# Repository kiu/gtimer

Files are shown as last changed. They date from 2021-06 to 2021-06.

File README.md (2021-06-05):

# gtimer
gtimer is a programmable controller for the GARDENA [Fully Automatic Flower Box Watering](https://www.gardena.com/int/products/watering/holiday-watering/fully-automatic-flower-box-watering/900916701/) drip system.
Thanks to an ATMEGA microcontroller and a RTC module very flexible watering plans can be achieved. In addition a temperature module influences the timings based on ambient temperature during the course of the day.

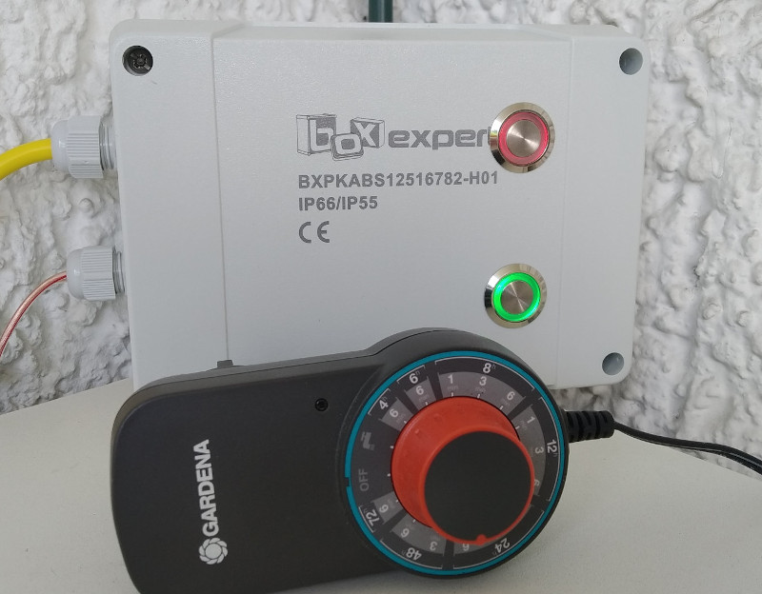
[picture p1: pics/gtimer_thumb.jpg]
gtimer


gtimer is a drop-in replacement for the GARDENA timer connecting to the original pump of the system.

# Warning
Be aware of what you are doing. You are playing with water and mains voltage in an outdoor environment.
Not only might this kill you, it will hurt the whole time you're dying.

# Nitty-Gritty Details
Checkout the [pics](https://github.com/kiu/gtimer/tree/master/pics) and [hardware](https://github.com/kiu/gtimer/tree/master/hardware) section including BOM, Schematic, PCB layout, firmware, etc.

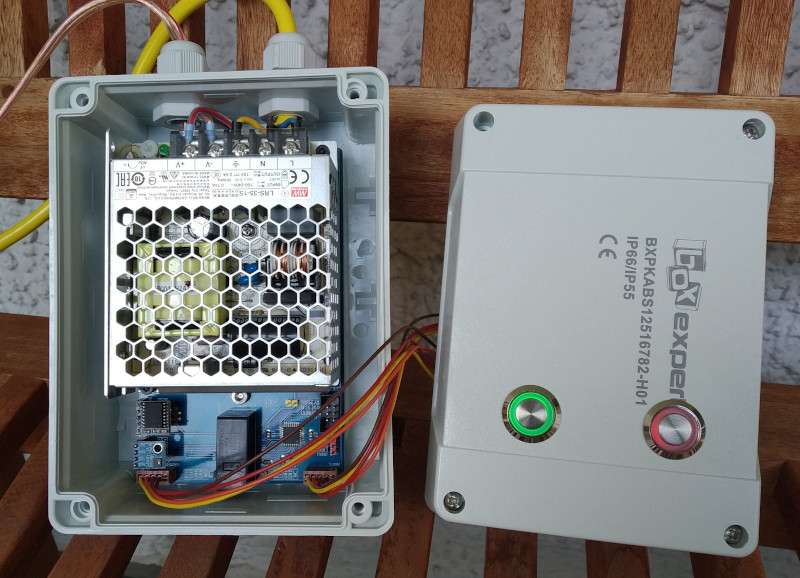
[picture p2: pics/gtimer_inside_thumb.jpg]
gtimer


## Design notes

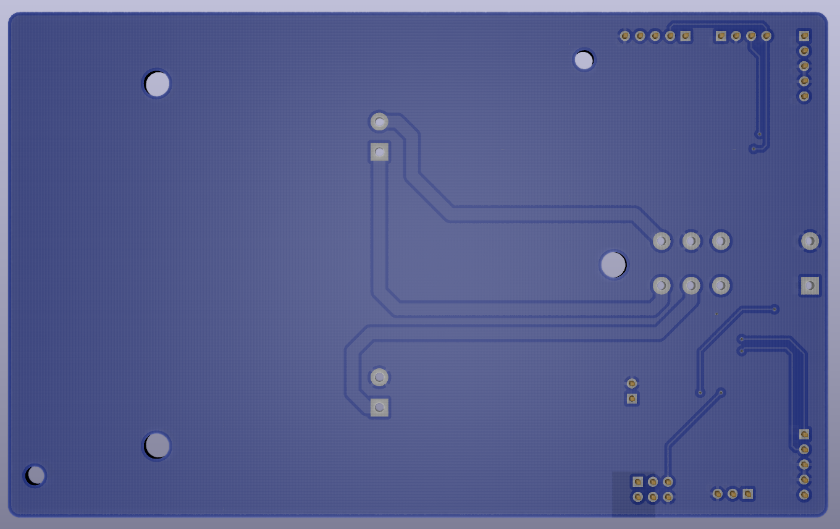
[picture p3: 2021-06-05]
hardware/kicad_gtimer_render_bottom.png

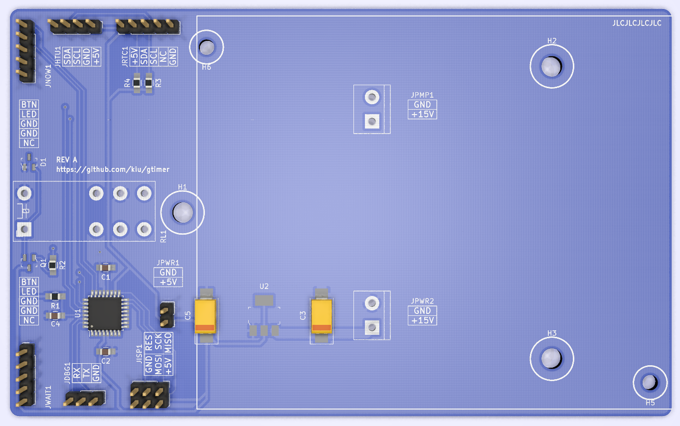
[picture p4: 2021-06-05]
hardware/kicad_gtimer_render_front.png

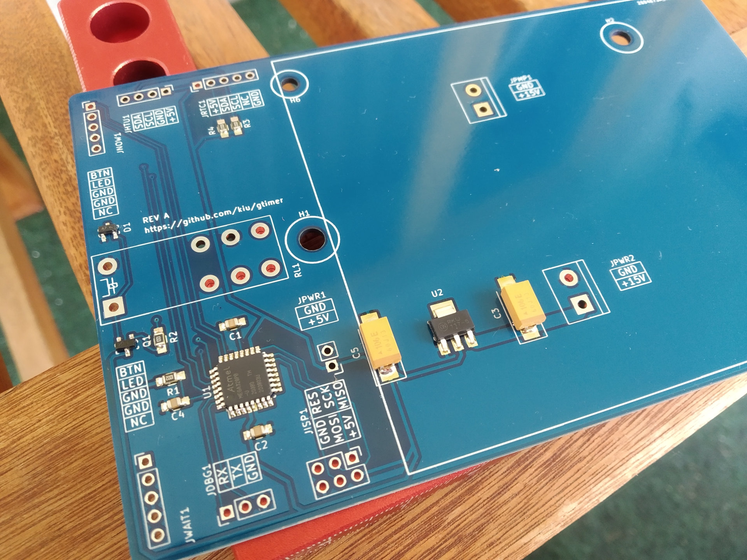
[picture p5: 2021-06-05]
pics/gtimer_reflow.jpg

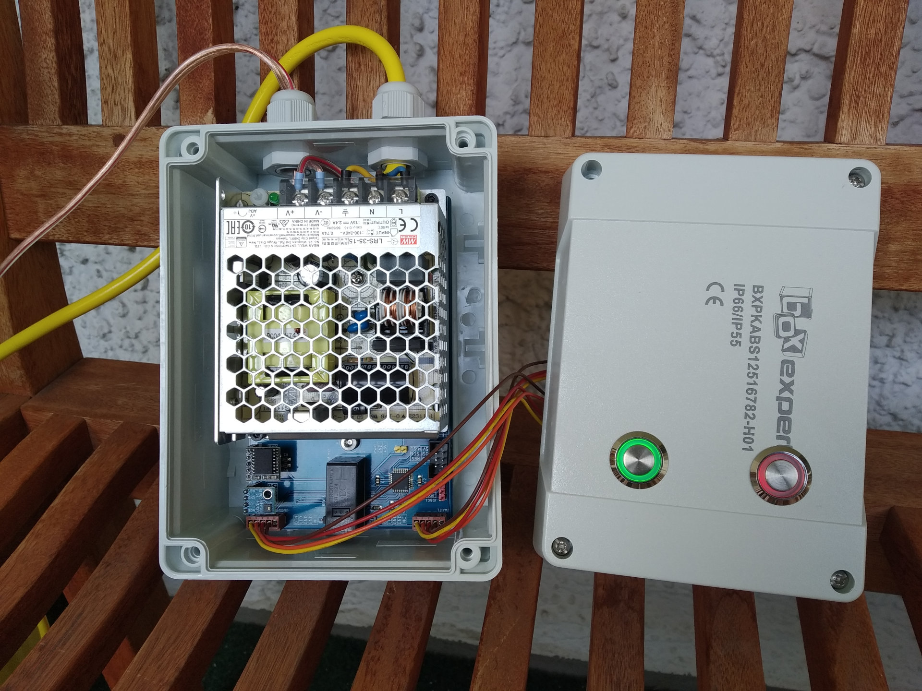
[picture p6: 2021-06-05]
pics/gtimer_inside.jpg

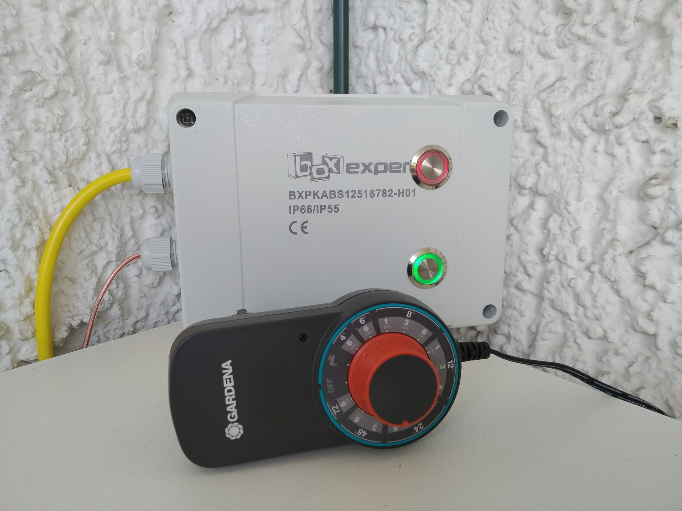
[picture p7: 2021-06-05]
pics/gtimer_comparison.jpg

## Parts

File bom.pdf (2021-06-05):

BOM

Page 1

Symbol | Description | Req | +VAT | Price | Price (sum) | Provider | ID
| | | | MOQ 1
U1 | ATMEGA 328PB-AU | 1 | 0 | 1,44 € | 1,44 € | http://reichelt.de | ATMEGA 328PB-AU
U2 | LDO 5V >=200mA | 1 | 0 | 0,36 € | 0,36 € | http://reichelt.de | NCP 1117 ST50T3G
Q1 | NPN Transitor >=100mA | 1 | 0 | 0,02 € | 0,02 € | http://reichelt.de | BC 847C SMD
D1 | Diode | 1 | 0 | 0,02 € | 0,02 € | http://reichelt.de | BAV 99 SMD
C3, C5 | 10uF/25V Tantalum D | 2 | 0 | 0,35 € | 0,70 € | http://reichelt.de | TAJ 7343 10/25
C1, C2, C4 | 100nF 0805 | 3 | 0 | 0,05 € | 0,15 € | http://reichelt.de | KEM X7R0805 100N
R1, R3, R4 | 10k 0805 | 3 | 0 | 0,02 € | 0,06 € | http://reichelt.de | RND 0805 1 10K
R2 | 1k 0805 | 1 | 0 | 0,02 € | 0,02 € | http://reichelt.de | RND 0805 1 1,0K
RL1 | Relay 5V | 1 | 0 | 2,60 € | 2,60 € | http://reichelt.de | G2RL-24 DC5
JNOW1, JWAIT1 | 1x05 Pin Header with cable | 2 | 0 | 0,67 € | 1,34 € | http://reichelt.de | PS 25/5G BR
JPMP1, JPWR2 | Terminal 1x02 5.08 | 2 | 0 | 0,25 € | 0,50 € | http://reichelt.de | CTB0509-2
JISP1 | Header 2x03 2.54 | 1 | 0 | 0,25 € | 0,25 € | http://reichelt.de | WSL 6G
JPWR1 | Header 1x02 2.54 | 1 | 0 | 0,05 € | 0,05 € | http://reichelt.de | MPE 087-1-002
JDBG1 | Header 1x03 2.54 | 1 | 0 | 0,08 € | 0,08 € | http://reichelt.de | MPE 087-1-003
JRTC1 | Socket 1x05 2.54 | 1 | 0 | 0,23 € | 0,23 € | http://reichelt.de | MPE 094-1-005
JHTU21 | Socket 1x04 2.54 | 1 | 0 | 0,17 € | 0,17 € | http://reichelt.de | MPE 094-1-004
- | 230V Power Cable | 1 | 0 | 4,30 € | 4,30 € | http://reichelt.de | NKSK 200 GE
- | Power Supply 15V >=2A | 1 | 0 | 11,07 € | 11,07 € | http://reichelt.de | MW LRS-35-15
- | Power Supply Protection | 1 | 0 | 0,34 € | 0,34 € | http://reichelt.de | TBC-05
- | Case 167x125x82mm | 1 | 0 | 10,10 € | 10,10 € | http://reichelt.de | HNS 12516782-H01
- | Cable 2x0,75mm 5m | 1 | 0 | 1,30 € | 1,30 € | http://reichelt.de | LAT 275-5
- | Connector | 1 | 0 | 1,30 € | 1,30 € | http://reichelt.de | DELOCK 65421
- | Standoff M3 10mm | 2 | 0 | 0,11 € | 0,22 € | http://reichelt.de | DI 10MM
- | Standoff M4 5mm | 3 | 0 | 0,09 € | 0,27 € | http://reichelt.de | VT DKM 5MM
- | Cable Gland PG9 | 2 | 0 | 0,65 € | 1,30 € | http://reichelt.de | LAPP 53018010
- | Cable Gland PG9 Fix | 2 | 0 | 0,40 € | 0,80 € | http://reichelt.de | LAPP 53019051
- | Aderendhülsen 0,75mm (11x) | 1 | 0 | 1,03 € | 1,03 € | http://reichelt.de | VT AEHI 0,75-100
- | Shipping reichelt.de | 1 | 0 | 5,95 € | 5,95 € | http://reichelt.de | -
(JHTU21) | GY-21 HTU21 Temperature Module | 1 | 0 | 5,99 € | 5,99 € | http://amazon.de | B07V9PJP1K
(JRTC1) | DS3231 RTC Module | 1 | 0 | 10,89 € | 10,89 € | http://amazon.de | B07QW2D4NF
- | Screw M3x5 | 4 | 0 | 0,00 € | 0,00 € | - | -
- | Screw M4x12 | 3 | 0 | 0,00 € | 0,00 € | - | -
(JNOW1, JWAIT1) | Push Button, 19mm, LED Red + Blue | 2 | 0 | 3,60 € | 7,20 € | http://aliexpress.com | 1005002351204813
- | PCB 138x85 + Stencil + Shipping + VAT | 1 | 0 | 37,33 € | 37,33 € | -

SUM
107,38 €
107,38 €

http://jlcpcb.com

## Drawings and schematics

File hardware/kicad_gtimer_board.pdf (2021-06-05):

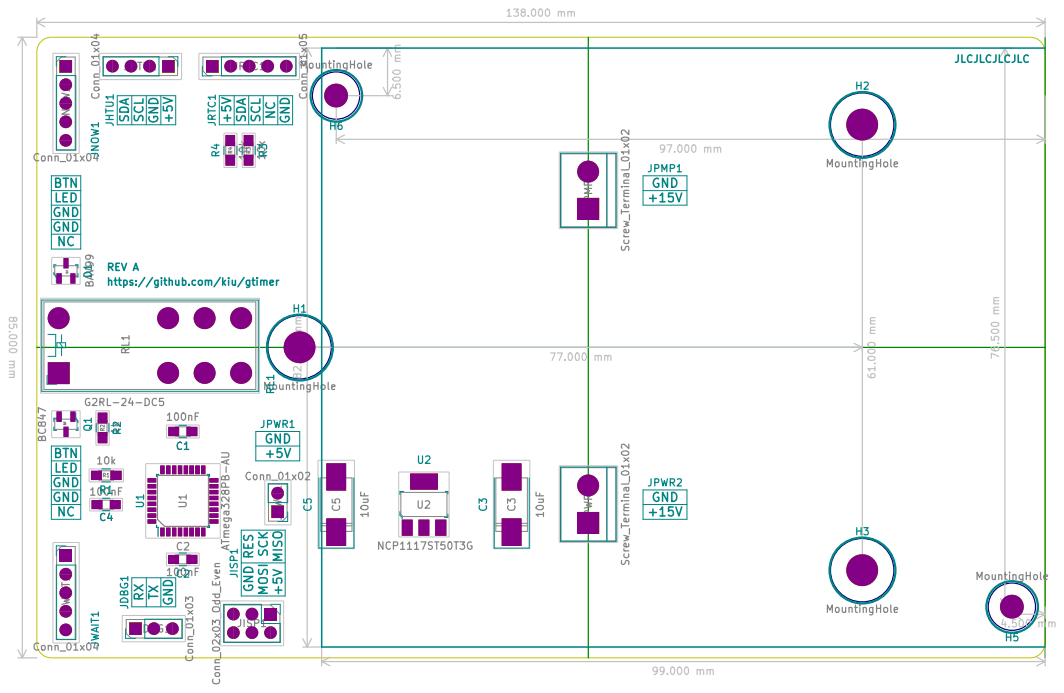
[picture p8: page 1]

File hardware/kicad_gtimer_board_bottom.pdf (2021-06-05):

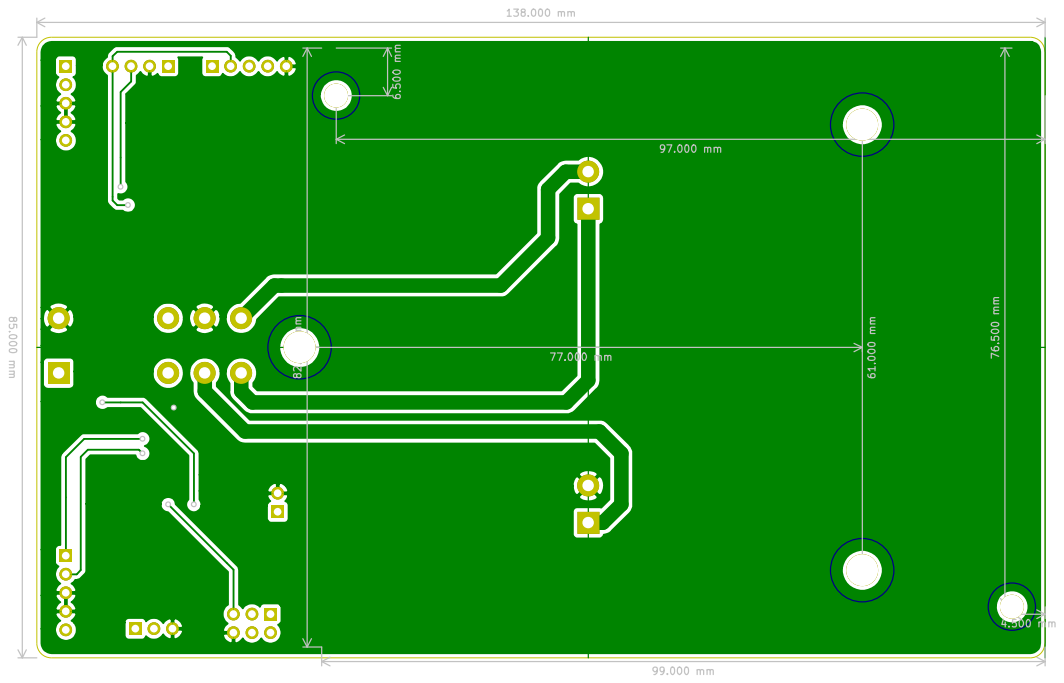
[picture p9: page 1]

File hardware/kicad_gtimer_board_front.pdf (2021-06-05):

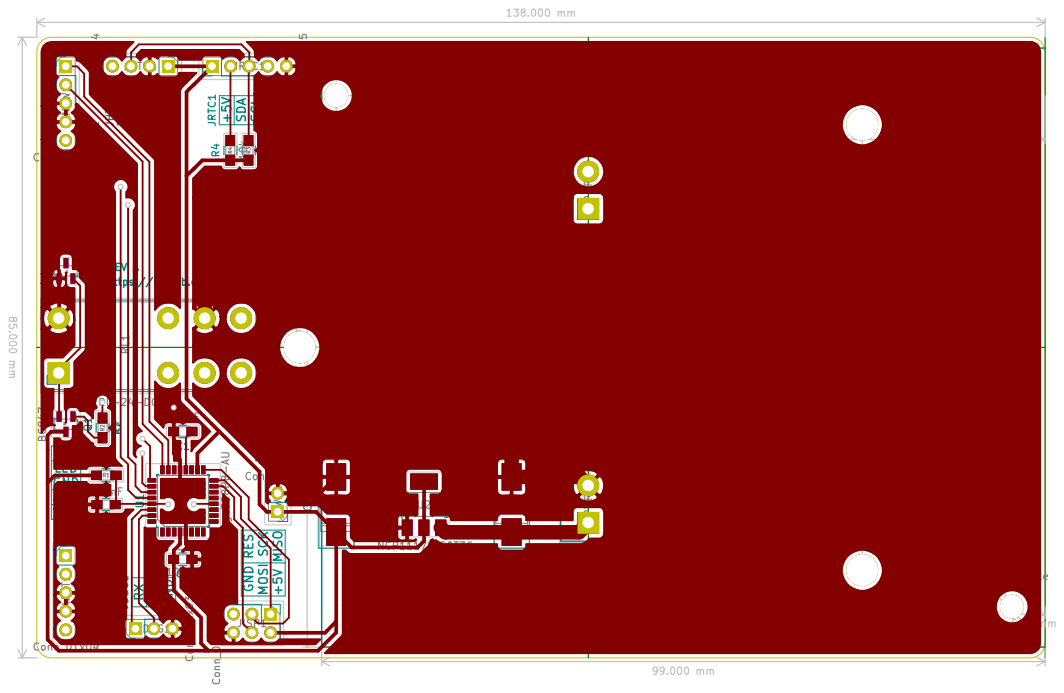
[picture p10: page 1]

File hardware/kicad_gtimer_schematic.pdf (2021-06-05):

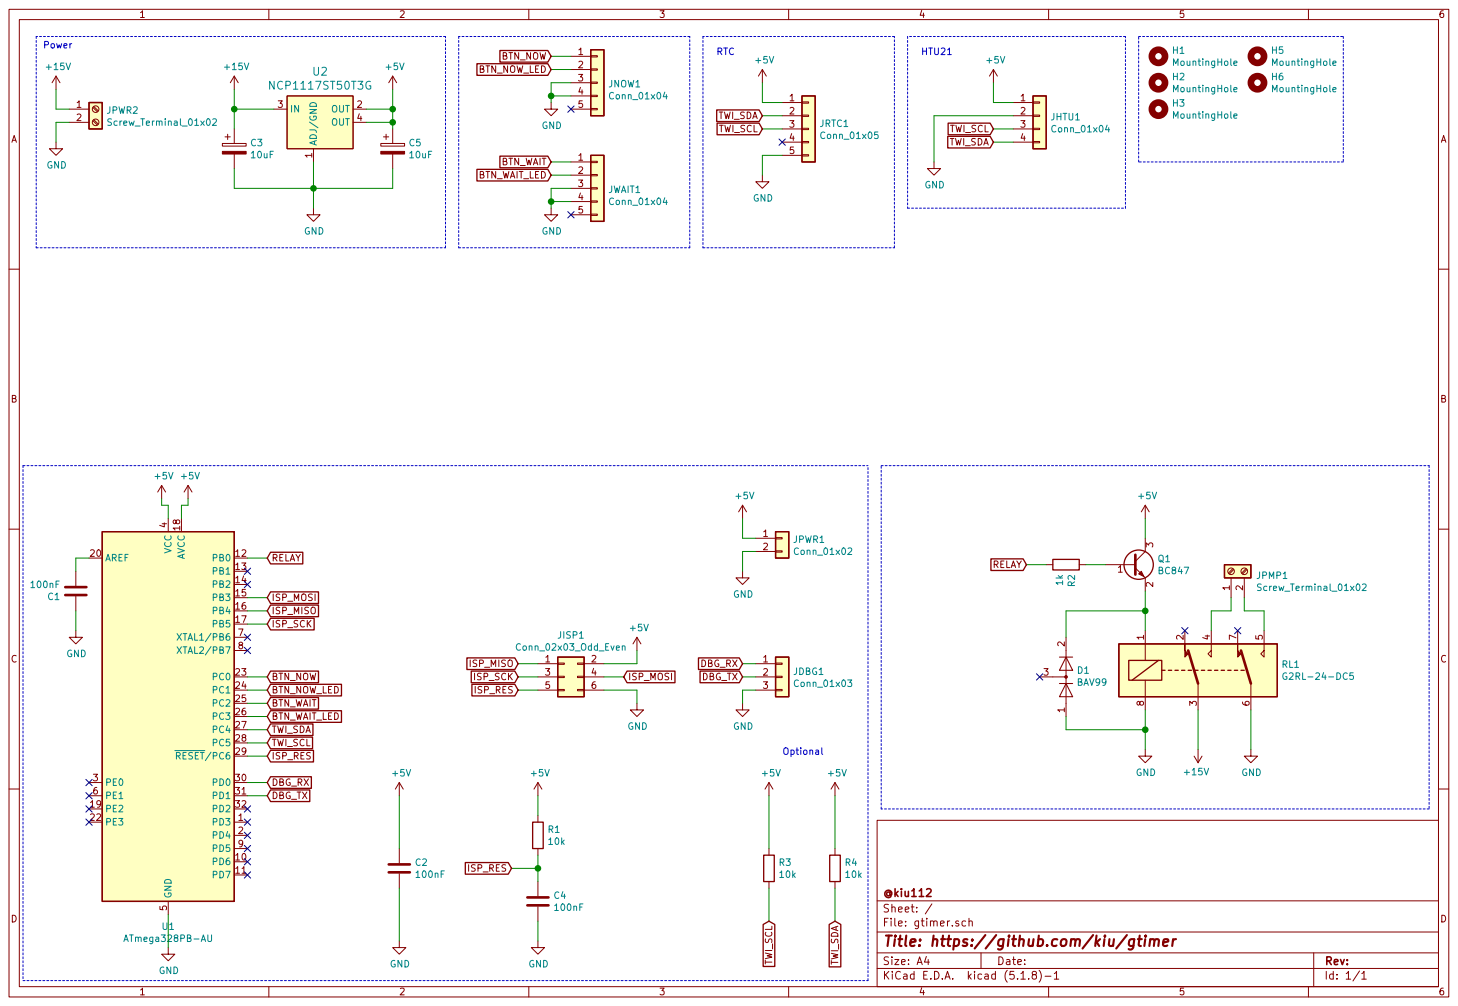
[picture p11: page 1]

File: gtimer.sch Sheet: / @kiu112

Id: 1/1 Title: https://github.com/kiu/gtimer

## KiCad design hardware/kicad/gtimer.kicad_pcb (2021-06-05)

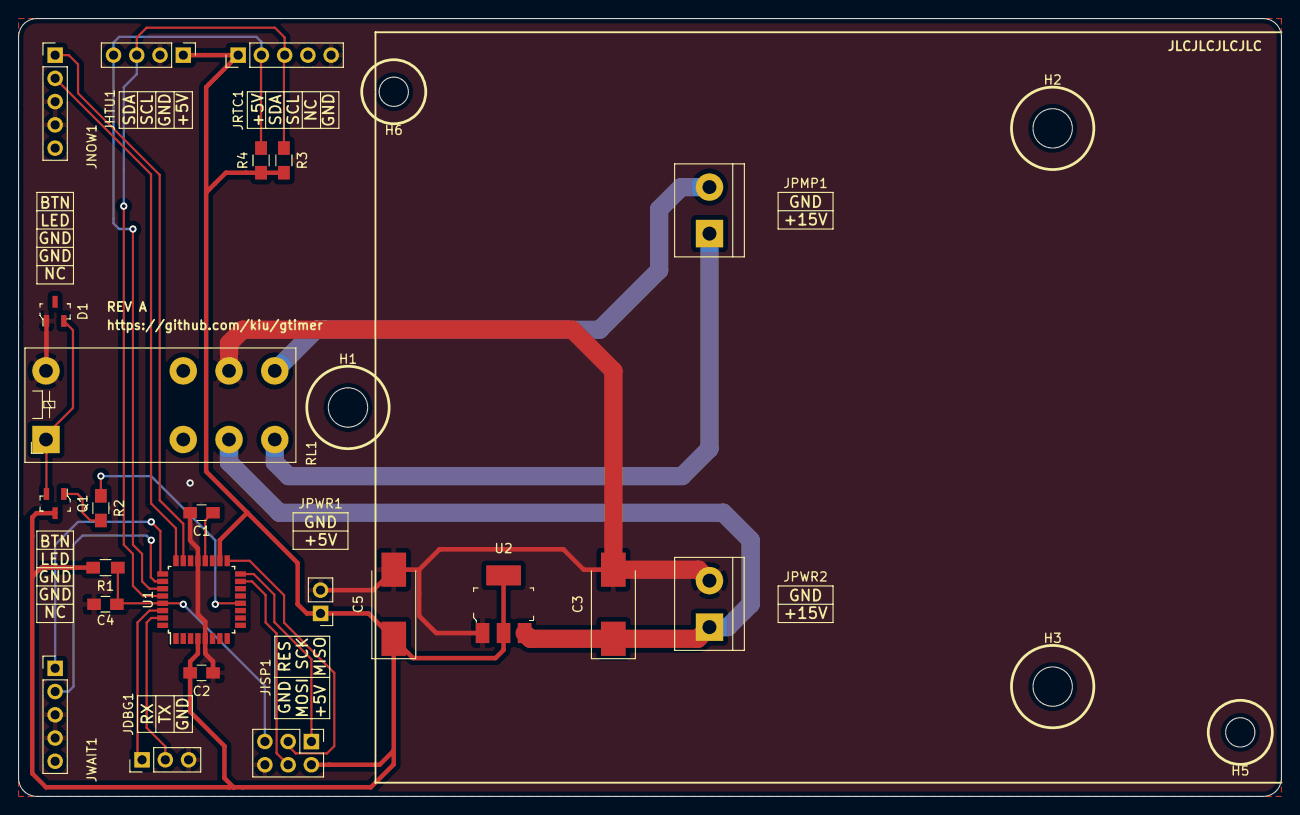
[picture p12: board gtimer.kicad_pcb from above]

Board: 2 copper layers, 138.0 x 85.0 mm, 28 parts (0 on the bottom side), 21 nets.

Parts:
C1, C2, C4: 100nF; C_0805_HandSoldering
C3, C5: 10uF; CP_Tantalum_Case-D_EIA-7343-31_Hand
D1: BAV99; SOT-23-3
H1, H2, H3: MountingHole; MountingHole_4.3mm_M4
H5, H6: MountingHole; MountingHole_3.2mm_M3
JDBG1: Conn_01x03; Pin_Header_Straight_1x03_Pitch2.54mm
JHTU1: Conn_01x04; Pin_Header_Straight_1x04_Pitch2.54mm
JISP1: Conn_02x03_Odd_Even; Pin_Header_Straight_2x03_Pitch2.54mm
JNOW1: Conn_01x04; Pin_Header_Straight_1x05_Pitch2.54mm
JPMP1: Screw_Terminal_01x02; TerminalBlock_bornier-2_P5.08mm
JPWR1: Conn_01x02; Pin_Header_Straight_1x02_Pitch2.54mm
JPWR2: Screw_Terminal_01x02; TerminalBlock_bornier-2_P5.08mm
JRTC1: Conn_01x05; Pin_Header_Straight_1x05_Pitch2.54mm
JWAIT1: Conn_01x04; Pin_Header_Straight_1x05_Pitch2.54mm
Q1: BC847; SOT-23-3
R1, R3, R4: 10k; R_0805_HandSoldering
R2: 1k; R_0805_HandSoldering
RL1: G2RL-24-DC5; Relay_DPDT_Omron_G2RL-24
U1: ATmega328PB-AU; LQFP-32_7x7mm_Pitch0.8mm
U2: NCP1117ST50T3G; SOT-223

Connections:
+5V: C2.1, C5.1, JHTU1.1, JISP1.2, JPWR1.1, JRTC1.1, Q1.3, R1.1, R3.1, R4.1, U1.4, U1.18, U2.2, U2.4
+15V: C3.1, JPWR2.1, RL1.3, U2.3
BTN_NOW: JNOW1.1, U1.23
BTN_NOW_LED: JNOW1.2, U1.24
BTN_WAIT: JWAIT1.1, U1.25
BTN_WAIT_LED: JWAIT1.2, U1.26
DBG_RX: JDBG1.1, U1.30
DBG_TX: JDBG1.2, U1.31
GND: C1.1, C2.2, C3.2, C4.2, C5.2, D1.1, JDBG1.3, JHTU1.2, JISP1.6, JNOW1.3, JNOW1.4, JPWR1.2, JPWR2.2, JRTC1.5, JWAIT1.3, JWAIT1.4, RL1.6, RL1.8, U1.5, U1.21, U2.1
ISP_MISO: JISP1.1, U1.16
ISP_MOSI: JISP1.4, U1.15
ISP_RES: C4.1, JISP1.5, R1.2, U1.29
ISP_SCK: JISP1.3, U1.17
unnamed: C1.2, U1.20
unnamed: D1.2, Q1.2, RL1.1
unnamed: JPMP1.1, RL1.4
unnamed: JPMP1.2, RL1.5
unnamed: Q1.1, R2.1
RELAY: R2.2, U1.12
TWI_SCL: JHTU1.3, JRTC1.3, R3.2, U1.28
TWI_SDA: JHTU1.4, JRTC1.2, R4.2, U1.27

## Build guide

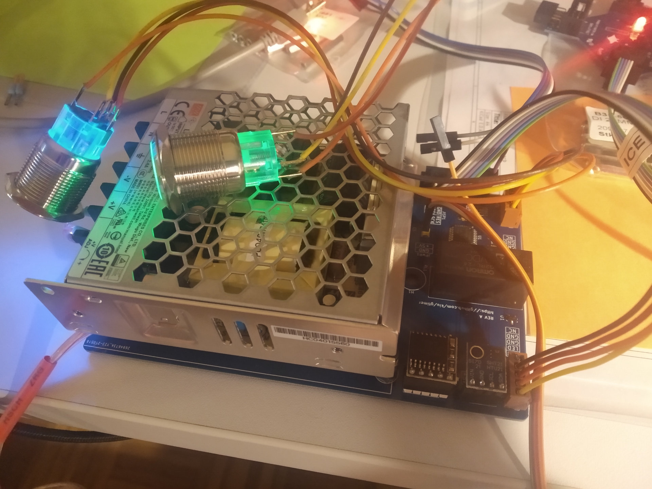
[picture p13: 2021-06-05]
pics/gtimer_assembly.jpg

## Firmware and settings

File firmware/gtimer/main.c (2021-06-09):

#include <atmel_start.h>
#include <util/delay.h>
#include <stdio.h>
#include "main.h"
#include "twihelper.h"

typedef enum {IDLE, START, RUN, STOP, WAIT, OFF} pump_mode_t;
const char *pump_mode_names[] = {"IDLE", "START", "RUN", "STOP", "WAIT", "OFF"};
	
pump_mode_t pump_mode = IDLE;
pump_mode_t pump_mode_next = IDLE;

uint8_t tempMax = 0;
uint8_t tempMaxLast = 0;

uint8_t humidityMax = 0;
uint8_t humidityMaxLast = 0;

uint8_t btn_now_debounce = 0xFF;
uint8_t btn_now_state = true;

uint8_t btn_wait_debounce = 0xFF;
uint8_t btn_wait_state = true;

uint16_t eeprom_index = 0;

volatile uint8_t pump_remaining = 0;

volatile uint8_t humidity_alarm = false;

volatile uint8_t t_hour = 0;
volatile uint8_t t_minute = 0;
volatile uint8_t t_second = 0;

volatile uint8_t triggerRTC = true;
volatile uint8_t triggerHTU = true;
volatile uint8_t triggerMidnight = false;

// ---------------------------------------------- ISR

ISR(TIMER1_COMPA_vect) {

	t_second++;
	if (t_second > 59) {
		t_second = 0;
		t_minute++;
		if (t_minute > 59) {
			t_minute = 0;
			t_hour++;
			if (t_hour > 23) {
				t_hour = 0;
			}
		}
	}	

	if (humidity_alarm) {
		BTN_NOW_LED_set_level(t_second % 2 == 0);
		BTN_WAIT_LED_set_level(t_second % 2 != 0);
	} else {
		if (pump_mode == RUN) {
			BTN_NOW_LED_set_level(t_second % 2 == 0);
		}
		if (pump_mode == WAIT) {
			BTN_WAIT_LED_set_level(t_second % 2 == 0);
		}
		if (pump_mode == OFF) {
			BTN_WAIT_LED_set_level(t_second % 4 == 0);
		}
	}

	if (pump_remaining > 0) {
		pump_remaining--;
	}

	if (pump_mode == RUN && pump_remaining == 0) {
		pump_mode_next = STOP;
	}

	if (t_second == 30) {
		triggerHTU = true;
	}

	if (t_second == 0) {
		
		if (t_minute == 15 || t_minute == 45) {
			triggerRTC = true;
		}
		
		if (t_minute == 0) {
			
			if (t_hour == 0) {
				triggerMidnight = true;
			}
			
			if (pump_mode == IDLE) {
				if (tempMax <= 22					&& ( t_hour == 15 ) ) {
					pump_mode_next = START;
				}
				if (tempMax > 22 && tempMax <=26	&& ( t_hour == 15 || t_hour == 21) ) {
					pump_mode_next = START;
				}
				if (tempMax > 26 && tempMax <=30	&& ( t_hour == 15 || t_hour == 18 || t_hour == 21 ) ) {
					pump_mode_next = START;
				}
				if (tempMax > 30					&& ( t_hour == 15 || t_hour == 18 || t_hour == 21 ) ) {
					pump_mode_next = START;
				}
				
				if (tempMaxLast > 30				&& ( t_hour == 9 ) ) {
					pump_mode_next = START;
				}
			}
		}		
	
	}

}

// ---------------------------------------------- Buttons

void btnNow() {
	printf("%02d:%02d:%02d Button: NOW\n", t_hour, t_minute, t_second);
	switch (pump_mode) {
		case IDLE:
			pump_mode_next = START;
			break;
		case START:
			break;
		case RUN:
			break;
		case STOP:
			break;
		case WAIT:
			pump_mode_next = IDLE;
			break;
		case OFF:
			pump_mode_next = WAIT;
			break;
	}
}

void btnWait() {
	printf("%02d:%02d:%02d Button: WAIT\n", t_hour, t_minute, t_second);
	switch (pump_mode) {
		case IDLE:
			pump_mode_next = WAIT;
			break;
		case START:
			pump_mode_next = STOP;
			break;
		case RUN:
			pump_mode_next = STOP;
			break;
		case STOP:
			pump_mode_next = WAIT;
			break;
		case WAIT:
			pump_mode_next = OFF;			
			break;
		case OFF:		
			break;
	}	
}

// ---------------------------------------------- HTU21

uint16_t readHTU21(uint8_t cmd) {
	uint16_t rawValue = 0;
	
	TWIStart();
	if (TWIGetStatus() != 0x08)	return 1;
	
	TWIWrite(0x80);
	if (TWIGetStatus() != 0x18)	return 2;
	
	TWIWrite(cmd);
	if (TWIGetStatus() != 0x28) return 3;
	
	TWIStart();
	if (TWIGetStatus() != 0x10)	return 4;
	
	TWIWrite(0x81);
	if (TWIGetStatus() != 0x40)	return 5;
	
	rawValue = (uint16_t)TWIReadACK() << 8;
	if (TWIGetStatus() != 0x50)	return 6;
	
	rawValue |= TWIReadACK();
	if (TWIGetStatus() != 0x50)	return 7;

	TWIReadNACK();
	if (TWIGetStatus() != 0x58)	return 8;
	
	TWIStop();

	rawValue &= ~(0x03);
	
	return rawValue;
}

uint16_t readTemperature() {
	uint16_t rawValue = readHTU21(0xE3);		
	float temperature = -46.85 + 175.72 * (float) rawValue / (float) ((uint32_t)1 << 16);
	if (temperature < 0) {
		temperature = 0;
	}
	return (uint8_t) temperature;
}

uint8_t readHumidity() {
	uint16_t rawValue = readHTU21(0xE3);
	float humidity = -6.0 + 125.0 * (float) rawValue / (float) ((uint32_t)1 << 16);
	if (humidity < 0) {
		humidity = 0;
	}
	return (uint8_t)humidity;
}

// ---------------------------------------------- DS3231

uint8_t writeDS3231(uint8_t cmd, uint8_t data) {
	TWIStart();
	if (TWIGetStatus() != 0x08)	return 1;
	
	TWIWrite(0xD0);
	if (TWIGetStatus() != 0x18)	return 2;

	TWIWrite(cmd);
	if (TWIGetStatus() != 0x28)	return 3;

	TWIWrite(data);
	if (TWIGetStatus() != 0x28)	return 4;
	
	TWIStop();
	
	return 0;
}

void setDS3231() {
	int hour, minute, second;
	printf("Compile Time: %s\n", __TIME__);
	sscanf(__TIME__, "%d:%d:%d", &hour, &minute, &second);

	second += SETRTC_OFFSET;
	if (second > 59) {
		second = 0;
		minute++;
		if (minute > 59) {
			minute = 0;
			hour++;
			if (hour > 23) {
				hour = 0;
			}
		}
	}
	printf("Setting RTC to %02d:%02d:%02d\n", hour, minute, second);
	printf("Setting Second: %d\n", writeDS3231(0x00, (second/10*16) + (second%10) ));
	printf("Setting Minute: %d\n", writeDS3231(0x01, (minute/10*16) + (minute%10) ));
	printf("Setting Hour: %d\n", writeDS3231(0x02, (hour/10*16) + (hour%10) ));
}

uint8_t readDS3231(uint8_t cmd) {
	uint8_t rawValue = 0;
	
	TWIStart();
	if (TWIGetStatus() != 0x08)	return 1;
	
	TWIWrite(0xD0);
	if (TWIGetStatus() != 0x18)	return 2;

	TWIWrite(cmd);
	if (TWIGetStatus() != 0x28)	return 3;
	
	TWIStart();
	
	TWIWrite(0xD1);
	if (TWIGetStatus() != 0x40) return 4;
	
	rawValue = (uint16_t)TWIReadNACK();
	if (TWIGetStatus() != 0x58)	return 5;

	TWIStop();
	
	return rawValue;
}

void syncRTC() {
	printf("%02d:%02d:%02d RTC update: ", t_hour, t_minute, t_second);
	
	uint8_t secRaw = readDS3231(0x00);
	uint8_t secValue = (secRaw >> 4) * 10 + (secRaw & 0b00001111);

	uint8_t minRaw = readDS3231(0x01);
	uint8_t minValue = (minRaw >> 4) * 10 + (minRaw & 0b00001111);

	uint8_t hrsRaw = readDS3231(0x02);
	uint8_t hrsValue = ((hrsRaw & 0b00110000) >> 4) * 10 + (hrsRaw & 0b00001111);

	t_second = secValue;
	t_minute = minValue;
	t_hour = hrsValue;

	printf("%02d:%02d:%02d\n", hrsValue, minValue, secValue);
}

// ---------------------------------------------- EEPROM

void eepromInit() {
	eeprom_index = (FLASH_0_read_eeprom_byte(0x3FE) << 8) + FLASH_0_read_eeprom_byte(0x3FF);
	printf("%02d:%02d:%02d EEPROM index: %d\n", t_hour, t_minute, t_second, eeprom_index);
}

void eepromWipe() {
	printf("%02d:%02d:%02d Clearing EEPROM ...", t_hour, t_minute, t_second);
	for (uint16_t i = 0; i < 0x3FF; i++) {
		FLASH_0_write_eeprom_byte(i, 0xFF);
	}
	
	FLASH_0_write_eeprom_byte(0x3FE, 0);
	FLASH_0_write_eeprom_byte(0x3FF, 0);	
	printf(" done\n");

	eepromInit();
}

void eepromUpdate(uint8_t t, uint8_t h) {
	FLASH_0_write_eeprom_byte(eeprom_index, t);
	eeprom_index++;
	FLASH_0_write_eeprom_byte(eeprom_index, h);
	eeprom_index++;
	if (eeprom_index >= 0x3FE) {
		eeprom_index = 0;
	}
	FLASH_0_write_eeprom_byte(0x3FE, eeprom_index >> 8);
	FLASH_0_write_eeprom_byte(0x3FF, eeprom_index);
	
	printf("%02d:%02d:%02d EEPROM new index: %d\n", t_hour, t_minute, t_second, eeprom_index);
}

void eepromDump() {
	printf("%02d:%02d:%02d EEPROM history\n", t_hour, t_minute, t_second);	
	printf("Day |Temp| Humid\n");
	
	uint16_t days = 0;
	
	for (uint16_t i = eeprom_index; i > 0; i-=2) {
		days++;
		printf("%04d %02dC %02d%%\n", days, FLASH_0_read_eeprom_byte(i - 2), FLASH_0_read_eeprom_byte(i - 1));
	}

	uint8_t tvalue = 0;
	uint8_t hvalue = 0;
		
	for (uint16_t i = 0x3FC; i > eeprom_index; i-=2) {
		days++;
		tvalue = FLASH_0_read_eeprom_byte(i);
		hvalue = FLASH_0_read_eeprom_byte(i + 1);
		if (tvalue != 0xFF || hvalue != 0xFF) {
			printf("%04d %02dC %02d%%\n", days, tvalue, hvalue);
		}
	}
	printf("\n");
}

// ---------------------------------------------- COMMANDS

void readCommands() {
	while(USART_0_is_rx_ready()) {
		char c = USART_0_read();
		switch (c) {
			case '?':
				printf("%02d:%02d:%02d Available commands\n", t_hour, t_minute, t_second);
				printf("\n");
				printf("m: Measure temperature and humidity\n");
				printf("z: Clear max temperature and humidity\n");
				printf("h: Show temperature and humidity history\n");				
				printf("e: Wipe temperature and humidity history\n");
				printf("\n");
				printf("s: Show humidity alarm status\n");
				printf("c: Turn humidity alarm off\n");
				printf("a: Turn humidity alarm on\n");
				printf("\n");
				printf("t: Show current time\n");
				printf("r: Sync time from RTC\n");
				printf("f: Trigger fake midnight\n");
				printf("\n");
				printf("n: Trigger NOW button\n");
				printf("w: Trigger WAIT button\n");
				printf("\n");
				printf("0: Turn pump off\n");
				printf("1: Turn pump on\n");
				printf("\n");
				break;

			case 'a':
			case 'A':
				printf("%02d:%02d:%02d Setting humidity alarm to ON\n", t_hour, t_minute, t_second);
				humidity_alarm = true;
				break;

			case 'c':
			case 'C':
				printf("%02d:%02d:%02d Setting humidity alarm to OFF\n", t_hour, t_minute, t_second);
				humidity_alarm = false;
				break;

			case 'e':
			case 'E':
				eepromWipe();
				break;

			case 'f':
			case 'F':
				triggerMidnight = true;
				break;

			case 'h':
			case 'H':
				eepromDump();
				break;

			case 'm':
			case 'M':
				triggerHTU = true;
				break;

			case 'n':
			case 'N':
				btnNow();
				break;

			case 'r':
			case 'R':
				triggerRTC = true;
				break;

			case 's':
			case 'S':
				printf("%02d:%02d:%02d Humidity alarm status: %d\n", t_hour, t_minute, t_second, humidity_alarm);
				break;

			case 't':
			case 'T':
				printf("%02d:%02d:%02d Time: %02d:%02d:%02d\n", t_hour, t_minute, t_second, t_hour, t_minute, t_second);
				break;

			case 'w':
			case 'W':
				btnWait();
				break;

			case 'z':
			case 'Z':
				printf("%02d:%02d:%02d Clearing max temperature and humidity\n", t_hour, t_minute, t_second);
				tempMax = 0;
				humidityMax = 0;
				break;

			case '0':
				printf("%02d:%02d:%02d Turning pump OFF\n", t_hour, t_minute, t_second);
				RELAY_set_level(false);
				break;

			case '1':
				printf("%02d:%02d:%02d Turning pump ON\n", t_hour, t_minute, t_second);
				RELAY_set_level(true);
				break;


		}
	}	
}

// ---------------------------------------------- MAIN

int main(void) {
	
	atmel_start_init();
	
	sei();
	
	printf("\nhttps://github.com/kiu/gtimer v0.2\n");
	printf("Enter '?' for available commands...\n\n");

	#if SETRTC
		setDS3231();
	#endif
	
	#if WIPEEEPROM
		eepromWipe();
	#endif

	eepromInit();
			
	BTN_NOW_LED_set_level(true);
	BTN_WAIT_LED_set_level(true);
	
	while(1) {
		
		if (triggerRTC) {
			triggerRTC = false;
			
			syncRTC();
		}
		
		if (triggerHTU) {
			triggerHTU = false;

			uint8_t tvalue = readTemperature();
			if (tvalue > tempMax) {
				tempMax = tvalue;
			}			

			uint8_t hvalue = readHumidity();
			if (hvalue > humidityMax) {
				humidityMax = hvalue;
			}
			
			printf("%02d:%02d:%02d M: %02dC (%02dC / %02dC) %02d%% (%02d%% / %02d%%)\n", t_hour, t_minute, t_second, tvalue, tempMax, tempMaxLast, hvalue, humidityMax, humidityMaxLast);
			
			if (hvalue > HUMIDITY_ALARM_THRESHOLD) {
				humidity_alarm = true;				
				pump_mode_next = STOP;
				printf("\n*** HUMIDITY ALARM ***\n");
			}
		}
		
		if (triggerMidnight) {
			triggerMidnight = false;

			printf("%02d:%02d:%02d Midnight\n", t_hour, t_minute, t_second);
			
			tempMaxLast = tempMax;
			tempMax = 0;
			
			humidityMaxLast = humidityMax;
			humidityMax = 0;
			
			if (pump_mode == WAIT) {
				pump_mode_next = IDLE;
			}
			
			eepromUpdate(tempMaxLast, humidityMaxLast);
		}
		
		btn_now_debounce = (btn_now_debounce << 1) + BTN_NOW_get_level();
		if (btn_now_state && btn_now_debounce == 0x00) {
			btn_now_state = false;
			btnNow();
		}
		if (!btn_now_state && btn_now_debounce == 0xFF) {
			btn_now_state = true;			
		}

		btn_wait_debounce = (btn_wait_debounce << 1) + BTN_WAIT_get_level();
		if (btn_wait_state && btn_wait_debounce == 0x00) {
			btn_wait_state = false;
			btnWait();
		}
		if (!btn_wait_state && btn_wait_debounce == 0xFF) {
			btn_wait_state = true;
		}
		
		if (pump_mode != pump_mode_next) {
			printf("%02d:%02d:%02d Pump mode change from %s to %s\n", t_hour, t_minute, t_second, pump_mode_names[pump_mode], pump_mode_names[pump_mode_next]);
			pump_mode = pump_mode_next;
			
			switch (pump_mode) {
				case IDLE:
					BTN_NOW_LED_set_level(true);
					BTN_WAIT_LED_set_level(true);
					break;
				case START:
					RELAY_set_level(true & !humidity_alarm);
					pump_remaining = PUMP_LENGTH;
					pump_mode_next = RUN;
					break;
				case RUN:
					break;
				case STOP:
					RELAY_set_level(false);
					pump_mode_next = IDLE;
					break;
				case WAIT:
					BTN_NOW_LED_set_level(true);
					BTN_WAIT_LED_set_level(true);
					break;
				case OFF:
					BTN_NOW_LED_set_level(true);
					BTN_WAIT_LED_set_level(true);
				break;
			}			
		}
			
		if (USART_0_is_rx_ready()) {
			readCommands();
		}
				
		_delay_ms(10);
	}

}

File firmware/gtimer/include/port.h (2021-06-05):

/**
 * \file
 *
 * \brief Tinymega Port related support
 *
 (c) 2020 Microchip Technology Inc. and its subsidiaries.

    Subject to your compliance with these terms,you may use this software and
    any derivatives exclusively with Microchip products.It is your responsibility
    to comply with third party license terms applicable to your use of third party
    software (including open source software) that may accompany Microchip software.

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
    IN NO EVENT WILL MICROCHIP BE LIABLE FOR ANY INDIRECT, SPECIAL, PUNITIVE,
    INCIDENTAL OR CONSEQUENTIAL LOSS, DAMAGE, COST OR EXPENSE OF ANY KIND
    WHATSOEVER RELATED TO THE SOFTWARE, HOWEVER CAUSED, EVEN IF MICROCHIP HAS
    BEEN ADVISED OF THE POSSIBILITY OR THE DAMAGES ARE FORESEEABLE. TO THE
    FULLEST EXTENT ALLOWED BY LAW, MICROCHIP'S TOTAL LIABILITY ON ALL CLAIMS IN
    ANY WAY RELATED TO THIS SOFTWARE WILL NOT EXCEED THE AMOUNT OF FEES, IF ANY,
    THAT YOU HAVE PAID DIRECTLY TO MICROCHIP FOR THIS SOFTWARE.
 *
 */

#ifndef PORT_INCLUDED
#define PORT_INCLUDED

#ifdef __cplusplus
extern "C" {
#endif

#include <compiler.h>
#include <stdint.h>
#include <stdbool.h>
#include <compiler.h>

enum port_pull_mode {
	PORT_PULL_OFF,
	PORT_PULL_UP,
};

enum port_dir {
	PORT_DIR_IN,
	PORT_DIR_OUT,
	PORT_DIR_OFF,
};

/**
 * \brief Set PORTB pin pull mode
 *
 * Configure pin to pull up, down or disable pull mode, supported pull
 * modes are defined by device used
 *
 * \param[in] pin       The pin number in PORTB
 * \param[in] pull_mode Pin pull mode
 */
static inline void PORTB_set_pin_pull_mode(const uint8_t pin, const enum port_pull_mode pull_mode)
{

	if (pull_mode == PORT_PULL_UP) {

		DDRB &= ~(1 << pin);

		PORTB |= 1 << pin;
	} else if (pull_mode == PORT_PULL_OFF) {

		PORTB &= ~(1 << pin);
	}
}

/**
 * \brief Set PORTB data direction
 *
 * Select if the port pins selected by mask data direction is input, output
 * or disabled.
 *
 * \param[in] mask      Bit mask where 1 means apply direction setting to the
 *                      corresponding pin
 * \param[in] direction PORT_DIR_IN  = Data direction in
 *                      PORT_DIR_OUT = Data direction out
 *                      PORT_DIR_OFF = Disables the pin
 *                      (low power state)
 */
static inline void PORTB_set_port_dir(const uint8_t mask, const enum port_dir direction)
{
	switch (direction) {
	case PORT_DIR_IN:
		DDRB &= ~mask;
		break;
	case PORT_DIR_OUT:
		DDRB |= mask;
		break;
	case PORT_DIR_OFF:
		DDRB &= ~mask;

		PORTB |= mask;
		break;
	default:
		break;
	}
}

/**
 * \brief Set PORTB single pin data direction
 *
 * Select if the pin data direction is input, output or disabled.
 * If disabled state is not possible, this function throws an assert.
 *
 * \param[in] pin       The pin number within PORTB (0..7)
 * \param[in] direction PORT_DIR_IN  = Data direction in
 *                      PORT_DIR_OUT = Data direction out
 *                      PORT_DIR_OFF = Disables the pin
 *                      (low power state)
 */
static inline void PORTB_set_pin_dir(const uint8_t pin, const enum port_dir direction)
{
	switch (direction) {
	case PORT_DIR_IN:
		DDRB &= ~(1 << pin);
		break;
	case PORT_DIR_OUT:
		DDRB |= 1 << pin;
		break;
	case PORT_DIR_OFF:
		DDRB &= ~(1 << pin);

		PORTB |= 1 << pin;
		break;
	default:
		break;
	}
}

/**
 * \brief Set PORTB level
 *
 * Sets output level on the pins defined by the bit mask
 *
 * \param[in] mask  Bit mask where 1 means apply port level to the corresponding
 *                  pin
 * \param[in] level true  = Pin levels set to "high" state
 *                  false = Pin levels set to "low" state
 */
static inline void PORTB_set_port_level(const uint8_t mask, const bool level)
{
	if (level) {
		PORTB |= mask;
	} else {
		PORTB &= ~mask;
	}
}

/**
 * \brief Set PORTB level
 *
 * Sets output level on a pin
 *
 * \param[in] pin       The pin number for device
 * \param[in] level true  = Pin level set to "high" state
 *                  false = Pin level set to "low" state
 */
static inline void PORTB_set_pin_level(const uint8_t pin, const bool level)
{
	if (level) {
		PORTB |= 1 << pin;
	} else {
		PORTB &= ~(1 << pin);
	}
}

/**
 * \brief Toggle out level on pins
 *
 * Toggle the pin levels on pins defined by bit mask
 *
 * \param[in] port  Ports are grouped into groups of maximum 32 pins,
 *                  PORT_PORTA = group 0, PORT_PORTB = group 1, etc
 * \param[in] mask  Bit mask where 1 means toggle pin level to the corresponding
 *                  pin
 */
static inline void PORTB_toggle_port_level(const uint8_t mask)
{
	PINB = mask;
}

/**
 * \brief Toggle output level on pin
 *
 * Toggle the pin levels on pin
 *
 * \param[in] pin       The pin number for device
 */
static inline void PORTB_toggle_pin_level(const uint8_t pin)
{
	PINB = 1 << pin;
}

/**
 * \brief Get input level on pins
 *
 * Read the input level on pins connected to a port
 *
 * \param[in] port  Ports are grouped into groups of maximum 32 pins,
 *                  PORT_PORTA = group 0, PORT_PORTB = group 1, etc
 */
static inline uint8_t PORTB_get_port_level(volatile uint8_t *port)
{
	return PINB;
}

/**
 * \brief Get level on pin
 *
 * Reads the level on a pin connected to a port
 *
 * \param[in] pin       The pin number for device
 */
static inline bool PORTB_get_pin_level(const uint8_t pin)
{
	return PINB & (1 << pin);
}

/**
 * \brief Write value to PORTB
 *
 * Write directly to the entire port register.
 *
 * \param[in] value   Value to write
 */
static inline void PORTB_write_port(const uint8_t value)
{
	PORTB = value;
}

/**
 * \brief Set PORTC pin pull mode
 *
 * Configure pin to pull up, down or disable pull mode, supported pull
 * modes are defined by device used
 *
 * \param[in] pin       The pin number in PORTC
 * \param[in] pull_mode Pin pull mode
 */
static inline void PORTC_set_pin_pull_mode(const uint8_t pin, const enum port_pull_mode pull_mode)
{

	if (pull_mode == PORT_PULL_UP) {

		DDRC &= ~(1 << pin);

		PORTC |= 1 << pin;
	} else if (pull_mode == PORT_PULL_OFF) {

		PORTC &= ~(1 << pin);
	}
}

/**
 * \brief Set PORTC data direction
 *
 * Select if the port pins selected by mask data direction is input, output
 * or disabled.
 *
 * \param[in] mask      Bit mask where 1 means apply direction setting to the
 *                      corresponding pin
 * \param[in] direction PORT_DIR_IN  = Data direction in
 *                      PORT_DIR_OUT = Data direction out
 *                      PORT_DIR_OFF = Disables the pin
 *                      (low power state)
 */
static inline void PORTC_set_port_dir(const uint8_t mask, const enum port_dir direction)
{
	switch (direction) {
	case PORT_DIR_IN:
		DDRC &= ~mask;
		break;
	case PORT_DIR_OUT:
		DDRC |= mask;
		break;
	case PORT_DIR_OFF:
		DDRC &= ~mask;

		PORTC |= mask;
		break;
	default:
		break;
	}
}
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

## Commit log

2021-06-05 Initial release
    [bom.ods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]
2021-06-05 Drill template
2021-06-05 Bugfix: It can't be 15:00, 18:00 and 21:00 at the same time. doh.
    [main.c]
2021-06-09 Adjusted timer interval and added RTC sync every 30m Added serial commands Added history of humidity measurements
